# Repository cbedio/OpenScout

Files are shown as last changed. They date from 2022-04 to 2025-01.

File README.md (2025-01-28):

# OpenScout Robot


          
 

## An Open Source Hardware Mobile Robot
OpenScout is a low-cost open source hardware and software mobile robot that can be used for both indoor and outdoor tasks, transporting up to 15kg of payload. The robot is designed to be easily and cheaply (350USD) buildable and modifiable by non-specialists, and to function as a new standard physical platform for robotics research and real-world tasks, replacing current proprietary options. Example applications include last mile and factory floor delivery, site survey and monitoring, and agricultural crop operations.

OpenScout is made of standard sizes aluminium extrusions making it very modular. That means its chassis design depends on the use case and the needs of the user. The robot provides the bare minimum (wizard-of-oz tele-operation and software for controlled differential drive) and future versions will introduce more chassis configurations, ROS/ROS2 integration and gazebo urdf files.

<p align="center" width="100%">
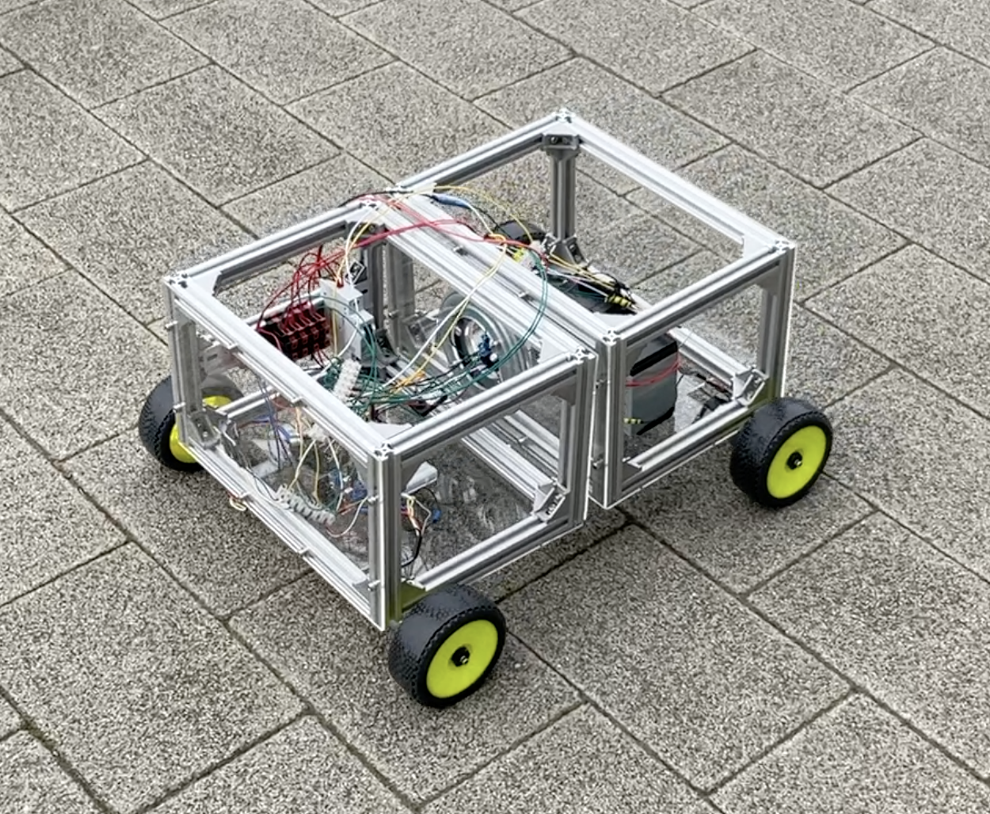
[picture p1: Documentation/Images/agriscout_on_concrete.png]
    
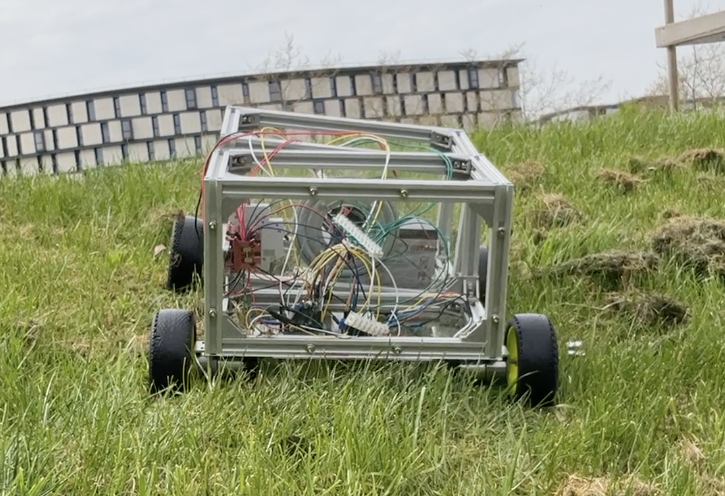
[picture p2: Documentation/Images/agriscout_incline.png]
     
</p>

For detailed changes, see the [CHANGELOG](CHANGELOG.md).

## Demonstration

Demonstrations showing a variety of different mobility aspects can be found in the [Demonstrations](Demonstrations) directory. The below demonstration shows OpenScout with a 'lazy Susan' revolute hinge successfully traversing uneven terrain with circa 40 mm divots.

https://user-images.githubusercontent.com/44243266/164105180-839fc627-df63-4446-af7d-90f431a007b9.mp4

## HackaDay
This project was covered in a [Hackaday article](https://hackaday.com/2022/09/26/robotic-platform-is-open-sourced-and-user-friendly/) by Bryan Cockfield, noting OpenScout as a straightforward and easy build without many specialized tools; providing a really useful platform to expand upon.

## Getting started
Materials used:
The robot consists of 200mm & 300mm 20x20 aluminium extrusions connected with 90 degree angle joints so the width, length and its height can be highly adjustable. We suggest also the [90:1 12V CQrobot](https://www.amazon.co.uk/CQRobot-90-Gearmotor-oz-Diameter/dp/B0887RR8SH) motor with encoder, as 4 of them provide enough traction to carry big payloads. Finally, an Arduino Mega is necessary as it provides enough interrupt pins for the RF receiver and the motor encoders.

The full bill of materials depends on each configuration and for more details please refer to the tutorials.

## Assembly Tutorial:

A fully documented assembly tutorial for the OpenScout with a 'Lazy Susan' revolute hinge is available below. Additionally, a comprehensive and fully annotated [Assembly Manual](Documentation/CAD_Files/Instruction_Manual/InstructionManual.pdf) with step by step 3D projections of the hardware build has been made available to print out. All associated CAD files and schematics are available in the [Documentation](Documentation) directory.

[OpenScout robot with 'Lazy Susan' revolute hinge](Hardware/robot_with_lazy_susan_bearing/README.md)

## How to contribute
While we try to keep this project open source you are free to make your own choice of materials and adapt the robot to your needs. However, we kindly request you to stick to the suggested 200mm & 300mm 20x20 aluminum extrusions, to allow other users disassemble their current configuration and try out yours! If you use OpenScout for your project, please open a PR with your configuration and tutorials. 

The general process of contributing on GitHub is widely documented however the outline process is below:

1. Identify where you want to host the project locally. This could be a OpenScout projects folder for example. 

1. Clone or fork the repository using GitHub desktop or the CLI into this location (CLI is recommended as this helps you become more familiar with Git in general). You can do this with the following command:

    ```bash
    git clone https://github.com/cbedio/OpenScout
    ```

1. Update the project and then make a pull request!

## License

This project is licensed under the [GNU General Public License v3.0](LICENSE) and [CERN-OHL-W](LICENCE) and [CC BY-SA](CC-BY-SA_LICENCE)

<p align="left" width="100%">
    
</p>

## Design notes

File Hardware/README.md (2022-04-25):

# OpenScout Assembly Tutorial

* [OpenScout with Lazy Susan bearing Assembly](robot_with_lazy_susan_bearing/README.md)

<p float="left">
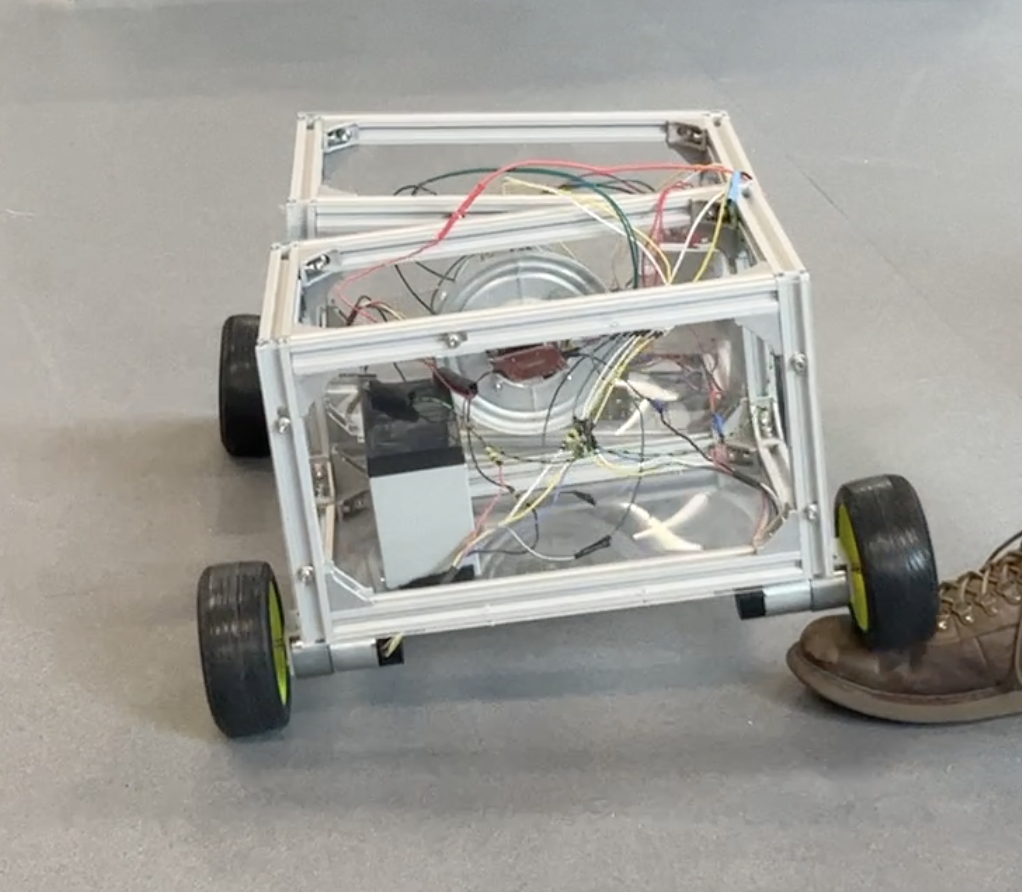
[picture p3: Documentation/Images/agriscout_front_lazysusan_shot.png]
Robot with hinge in the middle configuration
  
</p>

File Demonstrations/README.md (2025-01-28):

# Demonstrations

This folder contains a range of demonstration videos of the OpenScout to showcase its versatility, Lazy Susan mechanism, speed and agility as well as general movement capabilities. Additionally there is a video showing the simulated environment.

## 1 - OpenScout driving over a small slope

https://github.com/user-attachments/assets/b3fbb942-297d-4cb1-b123-8d51ed27b225

## 2 - OpenScout angular rotation

https://github.com/user-attachments/assets/c9248a99-090f-416c-b4d8-dba4bdea5ad4

## 3 - OpenScout moving with no payload

https://github.com/user-attachments/assets/f78b6c29-8d6c-4ecf-929b-bfc48b505c79

## 4 - OpenScout carrying 3kg

https://github.com/user-attachments/assets/6b9834aa-7cd8-4bb6-8bbc-55318a42252c

## 5 - OpenScout carrying 6kg

https://github.com/user-attachments/assets/0d55eaa9-31e6-48b6-9b8e-8ce0252e7a02

## 6 - OpenScout Simulation example run

https://github.com/user-attachments/assets/db36529f-7577-4ad0-a52f-730f6c3506c2

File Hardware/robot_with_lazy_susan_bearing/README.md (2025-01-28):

# Building the OpenScout robot with 'lazy Susan' revolute hinge
This configuration uses four-wheel differential drive steering, and a Lazy Susan hinged body which enables the wheels to drive over small obstacles without the need for suspension.

## Total Build time = 390 minutes (6 hours 30 minutes)

## Assembly Tools Required
These are the tools required to build the OpenScout

| Material | Quantity | UK link |
| ---|---:|:---:|
| M2/3/4/5 Hex Key | 1 | [Link](https://www.amazon.co.uk/ZISHATUO-Hex-Key-Set-2mm-5mm/dp/B09H768WYX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) |
| Small Flathead Screwdriver | 1 | [Link](https://www.amazon.co.uk/Rolson-28852-Screwdriver-Set-Pieces/dp/B00OOTPM6K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) |
| Small Phillips Head Screwdriver | 1 | [Link](https://www.amazon.co.uk/Rolson-28852-Screwdriver-Set-Pieces/dp/B00OOTPM6K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) |
| 100mm Steel rule | 1 | [Link](https://www.amazon.co.uk/Silverline-MT65-Steel-Rule-150/dp/B000LFXRNQ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) |

## Bill of materials
Before proceeding make sure you do have all the following materials. You are encouraged to read carefully the tutorial before starting building the robot.

For the chassis:
| Material | Quantity | Reference | UK link |
| ---|---:|:---:|:---:|
| 300mm 20x20 aluminium extrusion  | 8 |  A1 | [Link](https://ooznest.co.uk/product/v-slot-linear-rail-20x20mm-cut-to-size/) |
| 200mm 20x20 aluminium extrusion  | 17 | A2 | [Link](https://ooznest.co.uk/product/v-slot-linear-rail-20x20mm-cut-to-size/) |
| 20x20 Angle Joint Brace Brackets | 48 | B1 | [Link](https://amz.run/5TF6) |
| 90 Degree Cast Corner | 8 | B2 | [Link](https://ooznest.co.uk/product/90-degree-cast-corner/) |
| 200x340x3mm acrylic sheets | 4 | C1 | [Link](https://www.acrylicsheetcuttosize.co.uk/product/clear-acrylic-sheet/) |
| 240x340x3mm acrylic sheets | 2 | C2 | [Link](https://www.acrylicsheetcuttosize.co.uk/product/clear-acrylic-sheet/) |
| Lazy Susan 5.5in | 1 | LS | [Link](https://amz.run/5TF8) |
| Din rail with terminal blocks | 1 | DT | [Link](https://amz.run/5TFF) |
| Velcro 50mmx1m | 1 | Q | [Link](https://amz.run/5TFP) |
| 90:1 12V motor with encoders | 4 | M1 | [Link](https://amz.run/5TFQ) |
| Wheels (112x46mm) | 4 | M2 | [Link](https://www.amazon.co.uk/best-rubber-hexagon-offroad-crawler/dp/B08B16VQTZ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) |
| Wheel Hex Driver 12mm to 17mm | 4 | M3 | [Link](shorturl.at/axT25) |
| Hex coupler 6mm | 4 | M4 | [Link](https://amz.run/5TFT) |

For the electronics:
| Material | Quantity | Reference | UK link |
| ---|---:|:---:|:---:|
| 12V Lead Acid battery | 1 | E1 | [Link](https://uk.rs-online.com/web/p/lead-acid-batteries/0597835) |
| 10A circuit breaker | 1 | E2 | [Link](https://amz.run/5TFI) |
| Buck converter | 1 | E3 | [Link](https://amz.run/5TFJ) |
| Arduino Mega | 1 | E4 | [Link](https://amz.run/5TFL) |
| L298N Motor drivers | 2 | E5 | [Link](https://amz.run/5TFN) |
| Radio transmitter-receiver | 1 | E6 | [Link](https://amz.run/5TFO) |
| Breadboards | - | - | - |
| Wires | - | - | - |

Bolts & nuts:
| Material | Quantity | Reference | UK link |
| ---|---:|:---:|:---:|
| Sems screw 6mm (More info needed) | 16 | P4.6 | - |
| Sems screw 8mm (More info needed) | 8 | P4.8 | - |
| M4 8mm socket screw | 2 | S4.8 | - |
| M4 10mm socket screw | 8 | S4.10 | - |
| M4 12mm socket screw (More info needed) | 4 | S4.12 | - |
| M4 16mm socket screw (More info needed) | 4 | S4.16  | - |
| M4 30mm socket screw | 4 | S4.30 | - |
| M5 10mm socket screw | 144 | S5.10 | - |
| M4 T-slot nuts | 10 | T4 | - |
| M5 T-slot nuts | 144 | T5 | - |
| M4 Hex nuts | 12 | N1 | - |
| M4 Hammer nuts (More info needed)| 8 | N2 | - |
| M5 Washers | 170 | N3 | - |

<p float="left">
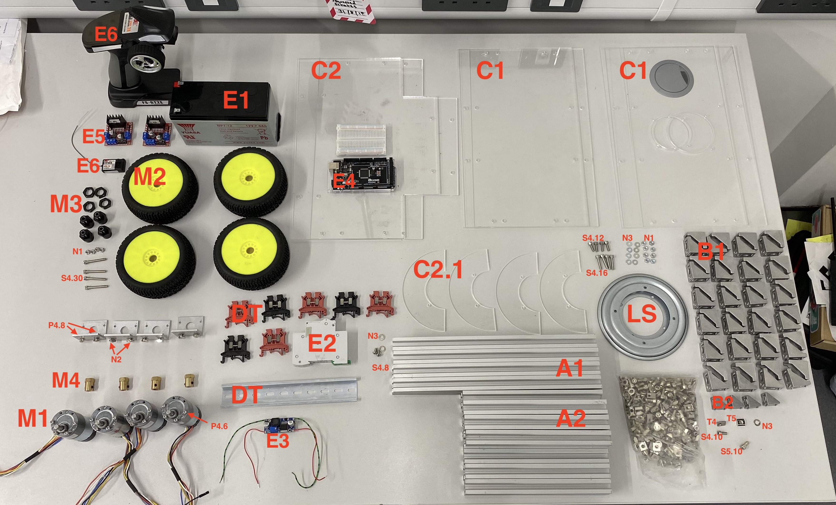
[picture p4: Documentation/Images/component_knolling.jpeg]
Open for full resolution
  
</p>

(**NOTE**: The links provided only as examples and there is no affiliation with the suppliers. The reader is advised to look for cheaper alternatives if possible. The motor brackets are provided in the CQRobot motor package, thus they are not in the bill of materials. Please keep in mind that alternative motors, brackets or components might require different bolts or additional parts.)

## Assembly instructions
This tutorial consists of 7 parts for constructing the robot platform with the hinge in the middle. It is necessary to be followed in the given order. After finishing the assembly, the robot is ready to be flashed with firmware!

Parts:
1. [Front compartment](./front_compartment.md)
2. [Back compartment](./back_compartment.md)
3. [Connecting the two compartments with the hinge](./hinge.md)
4. [Adding the acrylic panels](./acrylic_panels.md)
5. [Din rail](./din_rail.md)
6. [Attaching the motors and the wheels](./motors_and_wheels.md)
7. [Adding the electronics](./circuit_assembly_instructions.md)
8. [Assembling the system](./assembling_the_system.md)

## Adding the software
[Add the PID controller to the Arduino](../../Software/README.md)

## Speed PID controller calibration
[Speed PID controller calibration](./pid_calibration.md)

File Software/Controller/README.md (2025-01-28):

# Flashing Controller Software to the OpenScout Robot

## Install time = 5 minutes

The main script that needs to be uploaded to the Arduino board is located within the `Software` folder of this directory. To upload the sketch we recommend that you use the Arduino IDE, which can be obtained from [arduino.cc](https://www.arduino.cc/en/software).

## Getting started

1. Open the Arduino IDE and load in the `refined_pid.ino` file (`File -> Open -> select_file`).
1. Upload the sketch (see settings below)

### Settings

The firmware can be uploaded through `Sketch -> Upload` or by pressing the upload button.

Connect the Arduino board to the computer and set the port it is attached to:
  
- `Tools -> Board -> Arduino AVR Boards -> *Select the Arduino Board*`
- `Tools -> Processor -> *Select the Arduino Prosessor*`
- `Tools -> Port -> *Select the USB port*`

## Attribution

Github history lost due to moving files.

README.md updated by https://github.com/Rudi-Cato

Twist_via_MQTT.ino created by https://github.com/Rudi-Cato

refined_pid.ino created by https://github.com/Tobies-Cormac

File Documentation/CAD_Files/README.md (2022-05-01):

# Index of files

## DXF Files. These files are used for Laser Cutting

## STEP Files. These files can be modified in generic 3D CAD software

## Instruction Manual. Hard copy instructions for building the robot chassis

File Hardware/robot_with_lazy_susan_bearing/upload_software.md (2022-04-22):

# Flashing Controller Software to the AgriScout Robot

## Install time = 5 minutes

The main script that needs to be uploaded to the Arduino board is located within the `Software` folder of this directory. To upload the sketch we recommend that you use the Arduino IDE, which can be obtained from [arduino.cc](https://www.arduino.cc/en/software).

## Getting started

1. Open the Arduino IDE and load in the `simple_pid.ino` file (`File -> Open -> select_file`).
1. Upload the sketch (see settings below)

### Settings

The firmware can be uploaded through `Sketch -> Upload` or by pressing the upload button.


Connect the Arduino board to the computer and set the port it is attached to:
  
- `Tools -> Board -> Arduino AVR Boards -> *Select the Arduino Board*`
- `Tools -> Processor -> *Select the Arduino Prosessor*`
- `Tools -> Port -> *Select the USB port*`

## What's next?

Follow the [pid calibration](./pid_calibration.md) tutorial to fine tune the PID values for the speed control.

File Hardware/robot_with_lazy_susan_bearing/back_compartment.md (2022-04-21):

# Back Compartment

## Build time = 90 minutes

### Bill of materials:

| Material | Quantity | Reference | UK link |
| ---|---:|:---:|:---:|
| 300mm 20x20 aluminium extrusion  | 4 |  A1 | [Link](https://ooznest.co.uk/product/v-slot-linear-rail-20x20mm-cut-to-size/) |
| 200mm 20x20 aluminium extrusion  | 9 | A2 | [Link](https://ooznest.co.uk/product/v-slot-linear-rail-20x20mm-cut-to-size/) |
| 20x20 Angle Joint Brace Brackets | 24 | B1 | [Link](https://amz.run/5TF6) |
| 90 Degree Cast Corner | 8 | B2 | [Link](https://ooznest.co.uk/product/90-degree-cast-corner/) |
| M4 10mm socket screw | 8 | S4.10 | - |
| M5 10mm socket screw | 72 | S5.10 | - |
| M4 T-slot nuts | 8 | T4 | - |
| M5 T-slot nuts | 72 | T5 | - |
| M5 Washers | 80 | N3 | - |

## Introduction

The back compartment consists of a boxed-shaped construction which is almost identical to the front compartment. Its key difference is that it makes use of one extra (A2) extrusion on the right side of the box, to accommodate the din-rail which will be introduced later on. Also, the (A2) extrusion is fitted and attached using M4 (T4), (S4.10) nuts and screw with slightly smaller (B2) 90 degree joint brackets. The (T4) nut, does not need to be fitted through the open-ended (A2), instead it can be fitted in-place and fasting a screw on it will secure it (The fact that is fitted in-place though can be a bit tricky to properly secure it.)

## Step-by-step instructions

1. Duplicate the front compartment by following the previous tutorial ([front compartment](./front_compartment.md)) up to step 7, before fully connecting the two frames together. Ensure that the frame is constructed at the corners correctly and that the assembled parts look as in the following picture:

<p float="center">
  Attaching the front side with the back side of the back compartment
</p>

2. Attach 2 (B2) joints on each side on the spare (A2) extrusion on the right side of the compartment using the M4 parts. The (T4) nut can be fitted in-place, however adjusting it can be tricky. Try to align it an make it look as in the following picture. Screwing it tightly will hold it in-place as it rotates within the (A2).

3. Attach the piece prepared in the previous step on the construction. (Hint: A smaller allen key might help the ones with not so delicate hands.)

<p float="center">
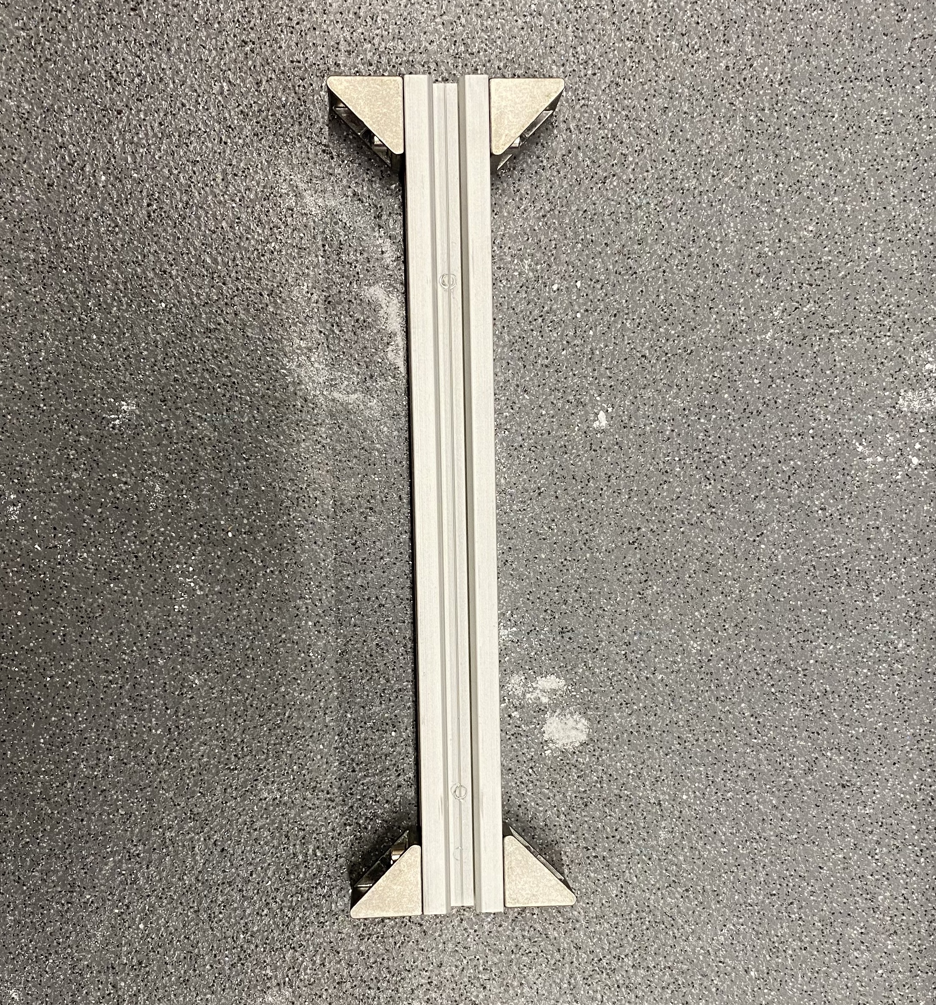
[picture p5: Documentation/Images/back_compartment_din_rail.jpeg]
This piece will host the din rail
  
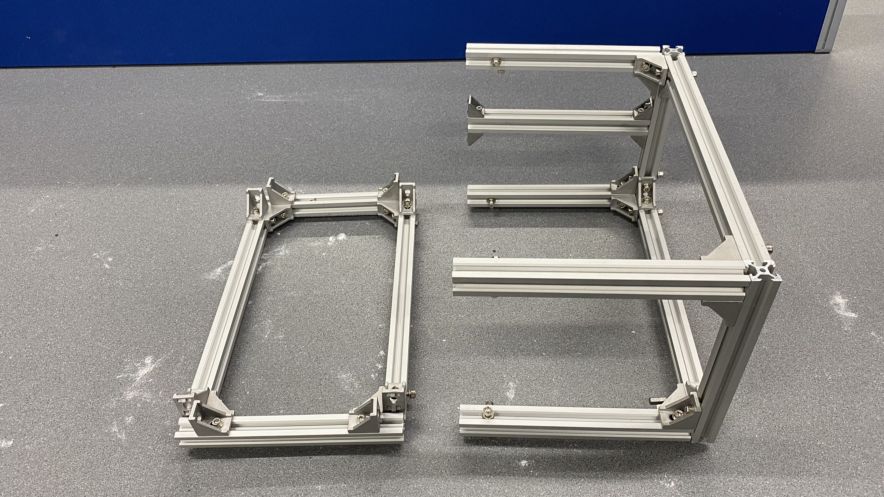
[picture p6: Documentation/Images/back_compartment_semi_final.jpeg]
Attaching the front side with the back side of the back compartment
  
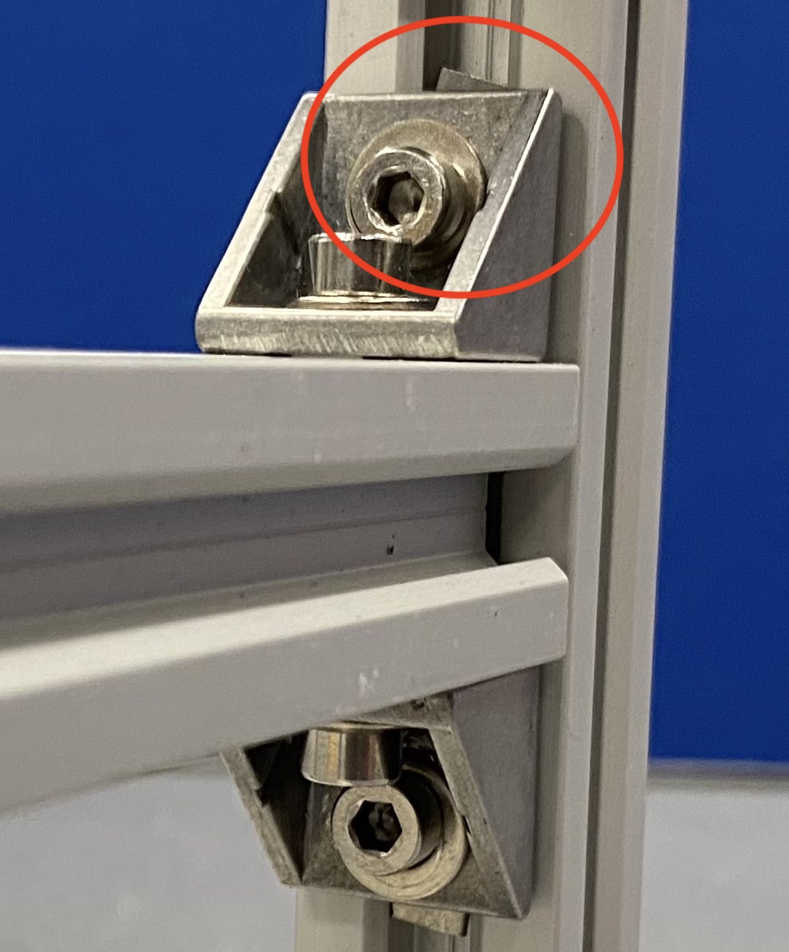
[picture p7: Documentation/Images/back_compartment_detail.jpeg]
Dir rail in detail
  
</p>

4. Fit the two frames together and tight the bolts together.
<p float="center">
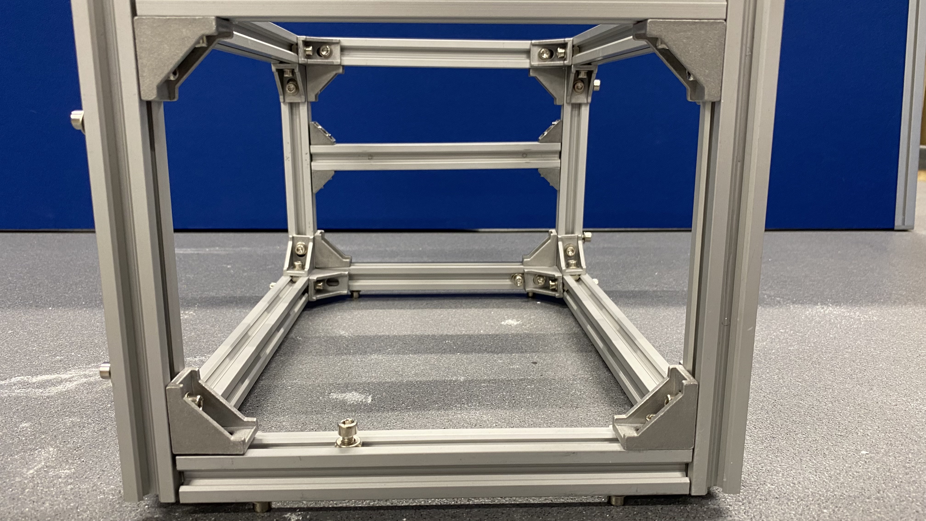
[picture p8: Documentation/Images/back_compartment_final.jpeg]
The back compartment fully assembled.
  
</p>

## What's next?
Follow the [lazy susan hinge](./hinge.md) tutorial to connect the front and the back compartment.

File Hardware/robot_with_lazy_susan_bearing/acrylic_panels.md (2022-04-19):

# Acrylic panels

## Build time = 20 minutes

### Bill of materials:

| Material | Quantity | Reference | UK link |
| ---|---:|:---:|:---:|
| 200x340x3mm acrylic sheets | 4 | C1 | [Link](https://www.acrylicsheetcuttosize.co.uk/product/clear-acrylic-sheet/) |
| 240x340x3mm acrylic sheets | 2 | C2 | [Link](https://www.acrylicsheetcuttosize.co.uk/product/clear-acrylic-sheet/) |

## Introduction

This tutorial includes instructions to laser-cut and fit the bare minimum acrylic panels needed on the robot. That is on the bottom, front and back side of the robot; in the previous tutorial, 2 sheets also were added in the middle as the hinge is attached on them. The reason is to keep the cost to the minimum, however the 3mm is not that strong as it should. You are welcome to use 5mm acrylic sheets, something stronger, or even wood to take full advantage of the maximum robot's payload.

## Step-by-step instructions

1. TODO: 
 - how to laser cut the bottom, front and back panels.
 - Upload the .dxf files in the `Documentation/CAD_Files` folder
 - Update the `Documentation/CAD_Files/README.md`

2. Fit the side panels (the smaller ones) as in the previous tutorial using the already equipped (S5.10) screws. (**HINT**: Fit first two opposing sides, and slide the panel across the extrusion, so you can align the misaligned (T5) nuts.)

<p float="center">
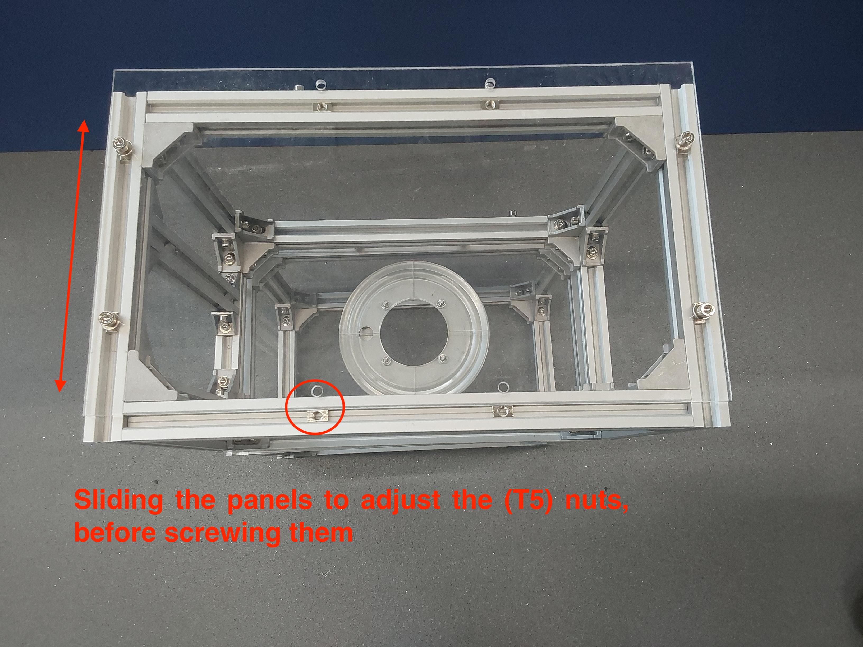
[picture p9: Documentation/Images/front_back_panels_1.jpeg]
Attaching the side panels
  
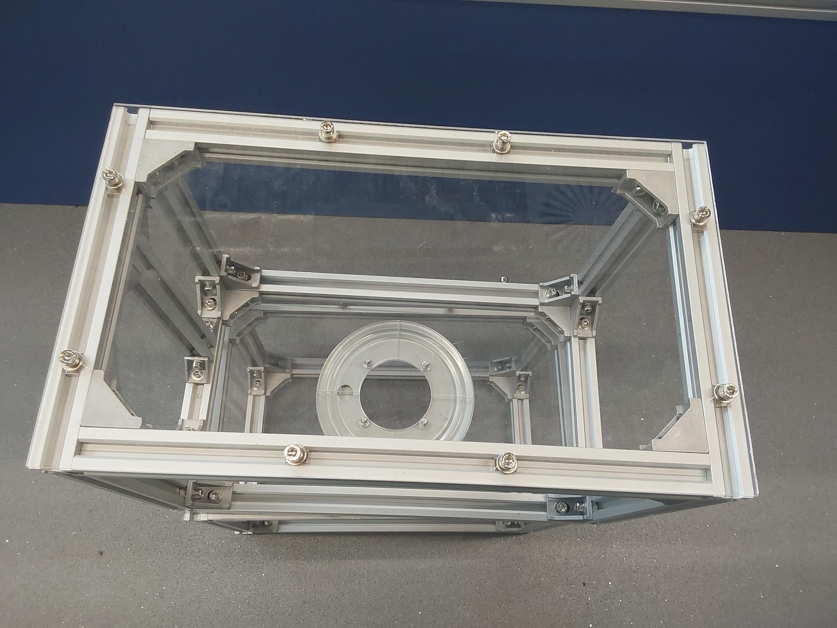
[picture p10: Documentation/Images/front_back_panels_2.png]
Attaching the side panels
  
</p>

3. Fit the bottom panels (the bigger ones) as in the previous step using the already equipped (S5.10) screws. The motor slots should be facing away from the middle. Repeat for each half of the construction. Make sure the construction is solid before progressing.

<p float="center">
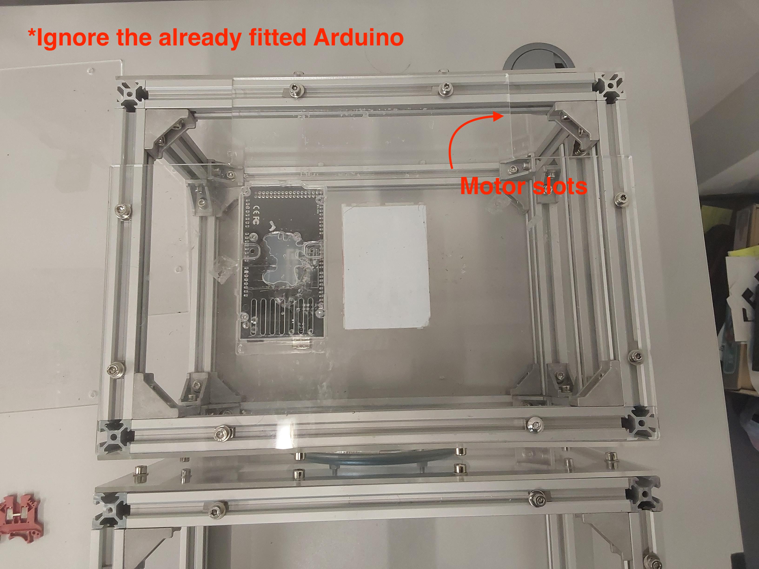
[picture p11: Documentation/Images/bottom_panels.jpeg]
Attaching the bottom panels
  
</p>

## What's next?

Follow the [din rail](./din_rail.md) tutorial to connect the front and the back compartment.

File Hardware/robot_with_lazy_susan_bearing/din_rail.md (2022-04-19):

# Din rail

## Build time = 15 minutes

### Bill of materials:

| Material | Quantity | Reference | UK link |
| ---|---:|:---:|:---:|
| Din rail with terminal blocks | 1 | DT | [Link](https://amz.run/5TFF) |
| Din rail with terminal blocks | 1 | DT | [Link](https://amz.run/5TFF) |
| 10A circuit breaker | 1 | E2 | [Link](https://amz.run/5TFI) |
| M4 8mm socket screw | 2 | S4.8 | - |
| M4 T-slot nuts | 2 | T4 | - |
| M5 Washers | 2 | N3 | - |

## Introduction

The din rail (DT) consists of a holed metal with some terminal blocks (red & white) attached on it. You can attach as many as you wish, and its purpose is provide some convience while wiring the battery.

## Step-by-step instructions

1. Attach the terminal blocks and the circuit breaker (E2) on the (DT). They 'click' if fitted properly, and they freely move along the rail.

<p float="center">
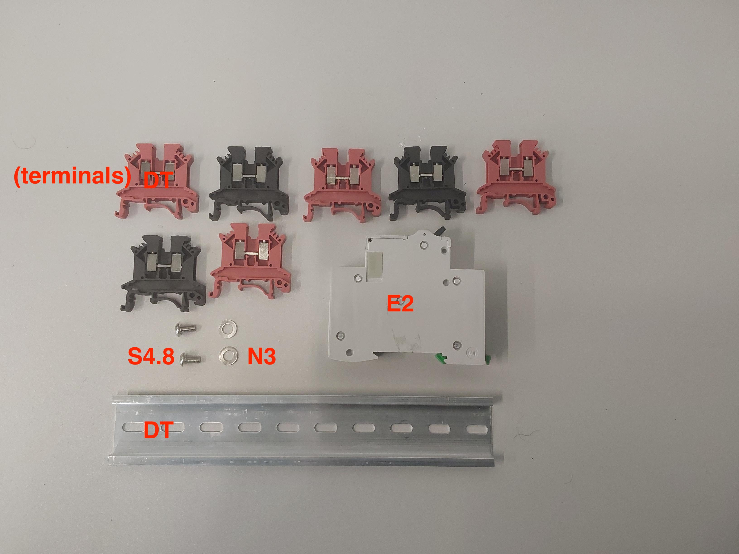
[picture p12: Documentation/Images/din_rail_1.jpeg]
Attaching the terminal blokcs on the din rail.
  
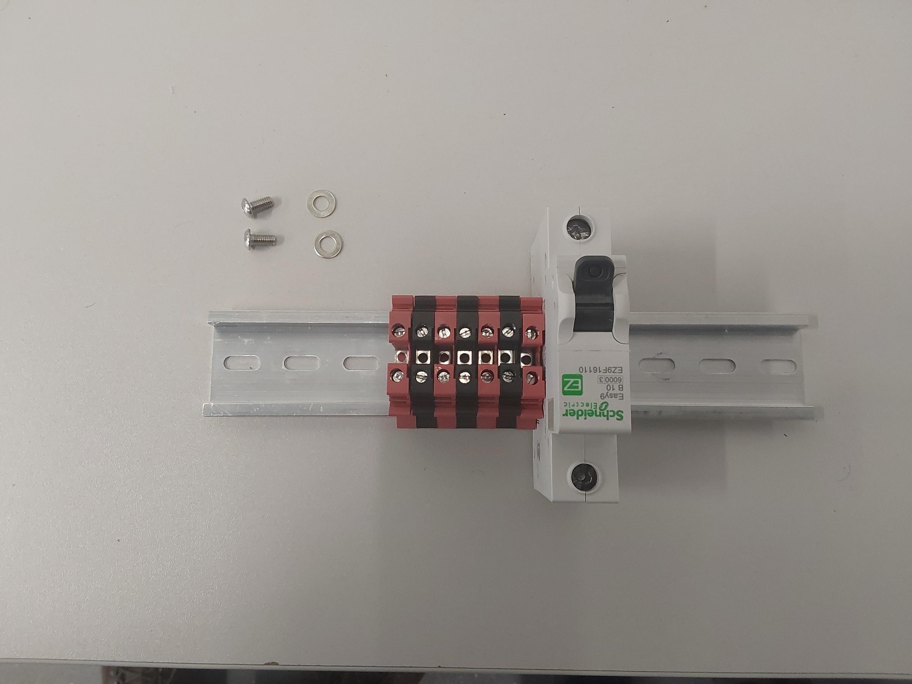
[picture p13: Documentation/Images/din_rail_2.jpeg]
The din rail assembled
  
</p>

2. Fit in-place 2 (T4) nuts on the extrusion that will accommodate the din rail and screw the rail on them using (N3) washers. Make sure that is properly fitted by giving it a shake.

<p float="center">
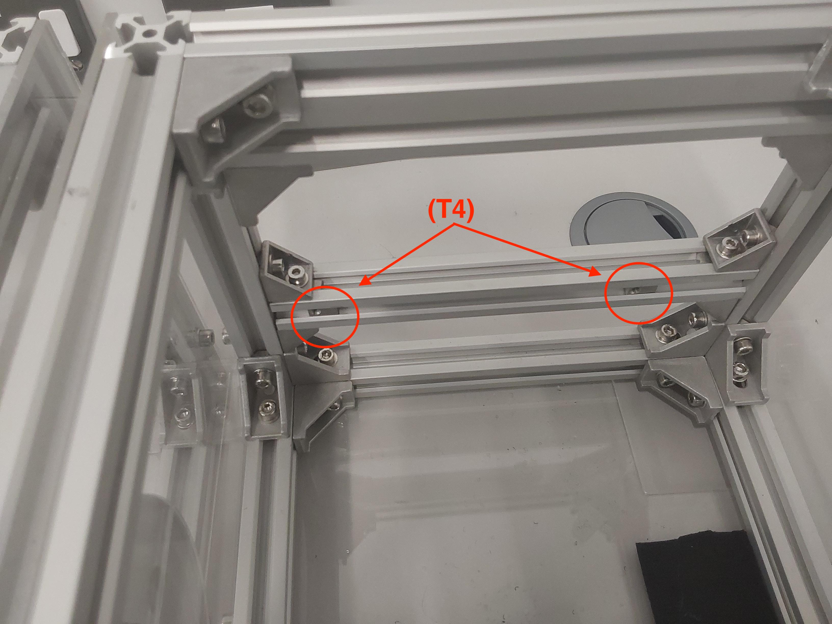
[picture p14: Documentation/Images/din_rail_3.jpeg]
Attaching the terminal blokcs on the din rail.
  
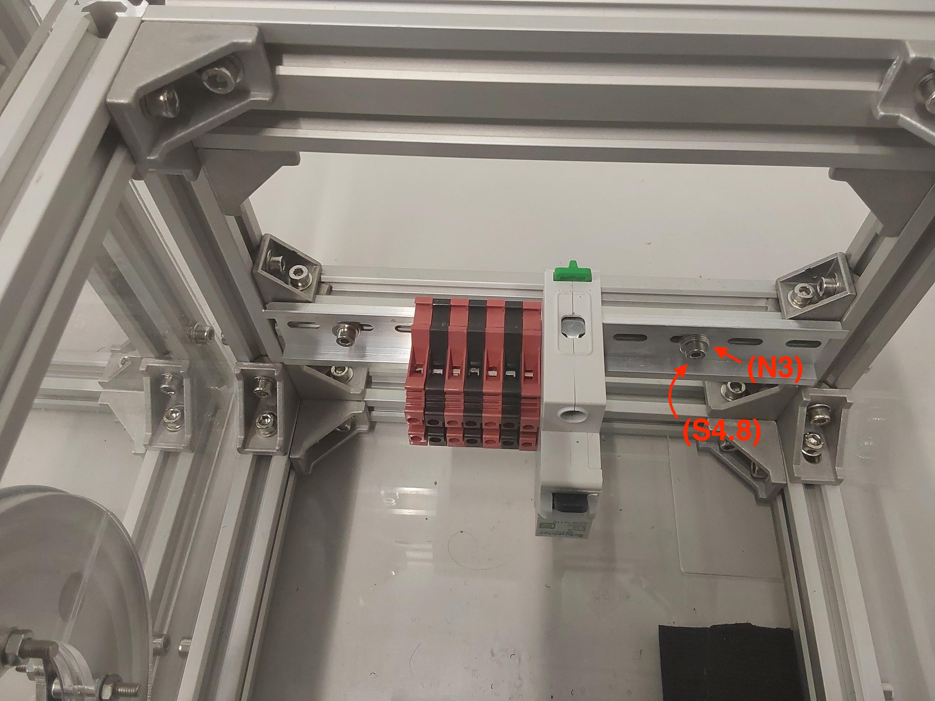
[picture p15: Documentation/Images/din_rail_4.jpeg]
The din rail assembled
  
</p>

## What's next?
Follow the [attaching motors and wheels](./motors_and_wheels.md) tutorial to complete the chassis of the robot.

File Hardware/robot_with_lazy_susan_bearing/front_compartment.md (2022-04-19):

# Front Compartment

## Build time = 75 minutes

### Bill of materials:

| Material | Quantity | Reference | UK link |
| ---|---:|:---:|:---:|
| 300mm 20x20 aluminium extrusion  | 4 |  A1 | [Link](https://ooznest.co.uk/product/v-slot-linear-rail-20x20mm-cut-to-size/) |
| 200mm 20x20 aluminium extrusion  | 8 | A2 | [Link](https://ooznest.co.uk/product/v-slot-linear-rail-20x20mm-cut-to-size/) |
| 20x20 Angle Joint Brace Brackets | 24 | B1 | [Link](https://amz.run/5TF6) |
| M5 10mm socket screw | 72 | S5.10 | - |
| M5 T-slot nuts | 72 | T5 | - |
| M5 Washers | 72 | N3 | - |

<p float="left">
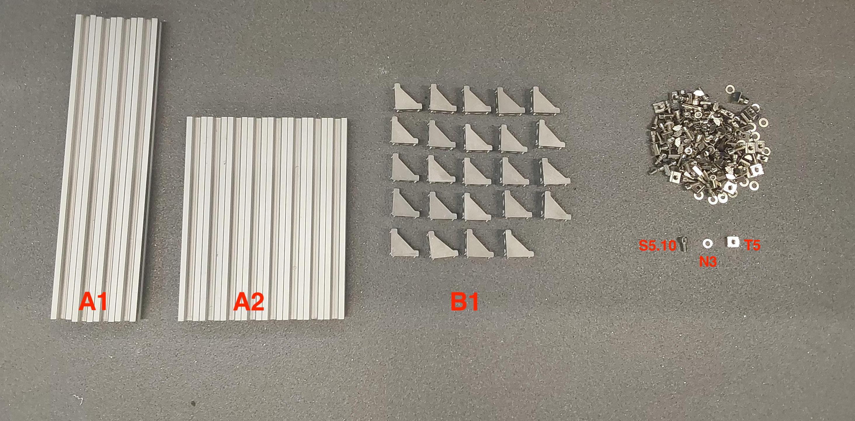
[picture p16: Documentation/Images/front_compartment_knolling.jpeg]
Open for full resolution
  
</p>

## Introduction

The front compartment consists of a boxed-shaped construction made of x4 300mm aluminium extrusions (A1) in horizontal positions (giving width to the box), x4 200mm (A2) extrusions (giving length to the box) and x4 (A2) extrusions vertically attached (giving height to the box). The following image shows how it should look like if completed successfully. Notice how the extrusions are attached together using 3 angle joints (red circle) (B1) on each corner (8 corners in total). Furthemore, the compartment is symmetrical across all 3 major axis. The blue circles indicate bolts which will accommodate the acrylic panels (8 bolts in total in the bottom, front and back sides of the compartment. The top and the left/right sides do not accommodate acrylic panels currently to lower the cost.).

Final result:
<p float="left">
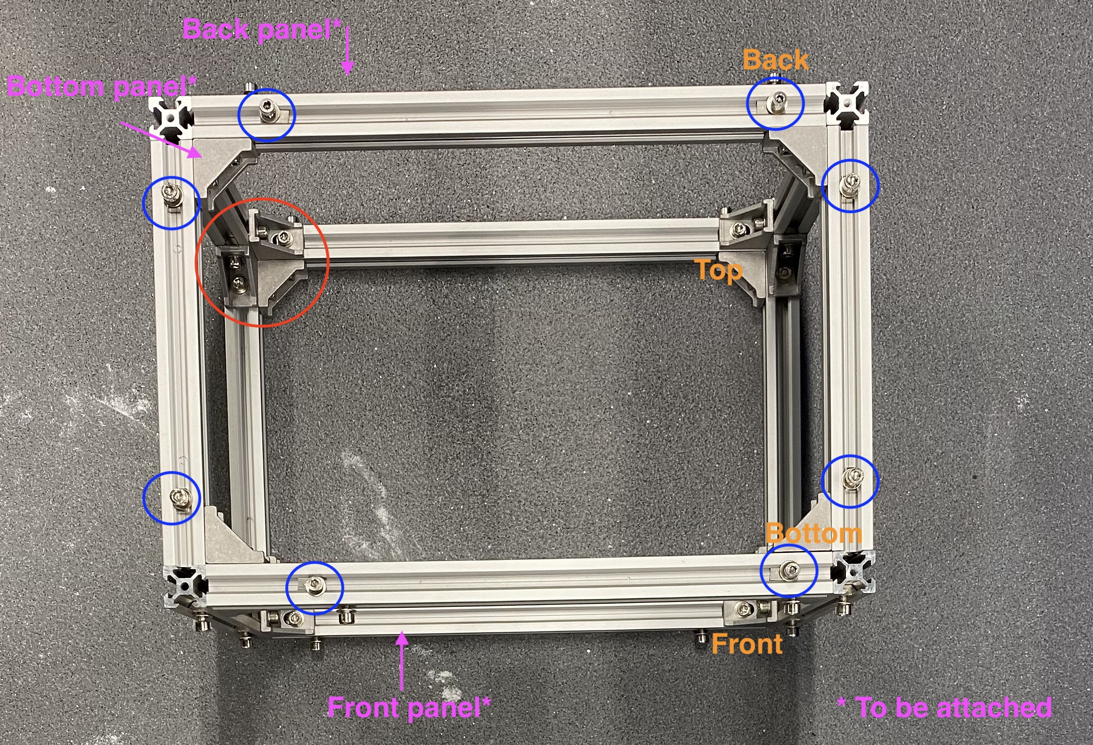
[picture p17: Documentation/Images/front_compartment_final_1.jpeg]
Resulting front compartment
  
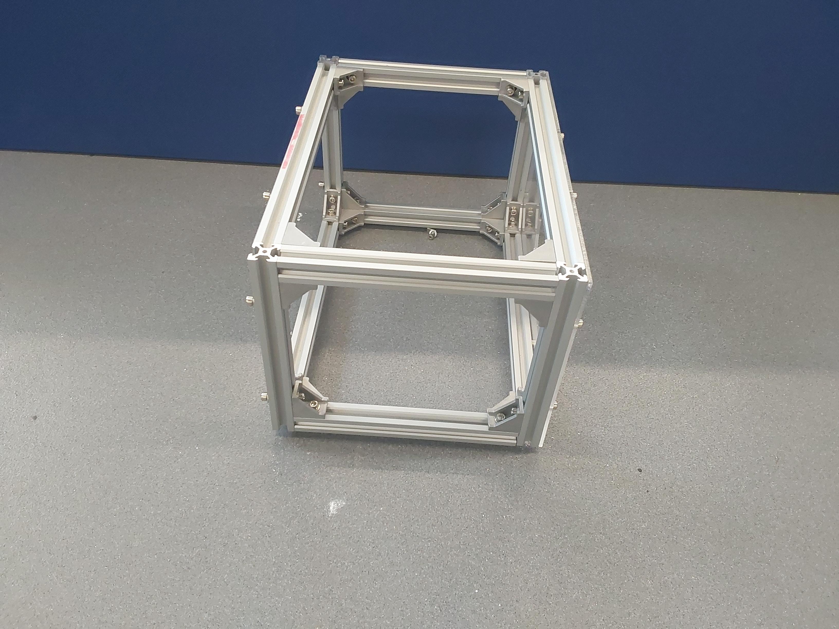
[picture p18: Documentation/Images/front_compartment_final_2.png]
Resulting front compartment
  
</p>

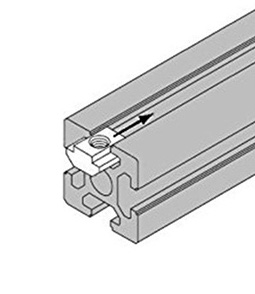
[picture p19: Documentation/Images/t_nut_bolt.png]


The T-slot nut (T5) is very useful to fasten things on aluminium extrusions as it allows it to freely slide within the extrusion and gets secured once it's fastened with a screw. The order of attachment from bottom to top should be: T-slot nut (T5), attachment, washer (N3) and lastly secured with the bolt (S5.10). **Be careful though that the T-nut to be inserted needs an open ended extrusion, so you need to know how many of them you need before start attaching things to the end of the extrusions.**

## Step-by-step instructions

1. Prepare 4 (A2) extrusions which are going to be used vertically defining the height of the robot. Attach the (B1) joints using the order defined previously: (T5) nut, (B1) joint, (N3) washer, and secure with a (S5.10) socket screw. Each side should have 2 joints attached and a (S5.10) without something attached (these sockets will later accommodate the acrylic panels). Do not tight the screws too much as this is not their final place. Just try to secure them on the aluminium.

<p float="center">
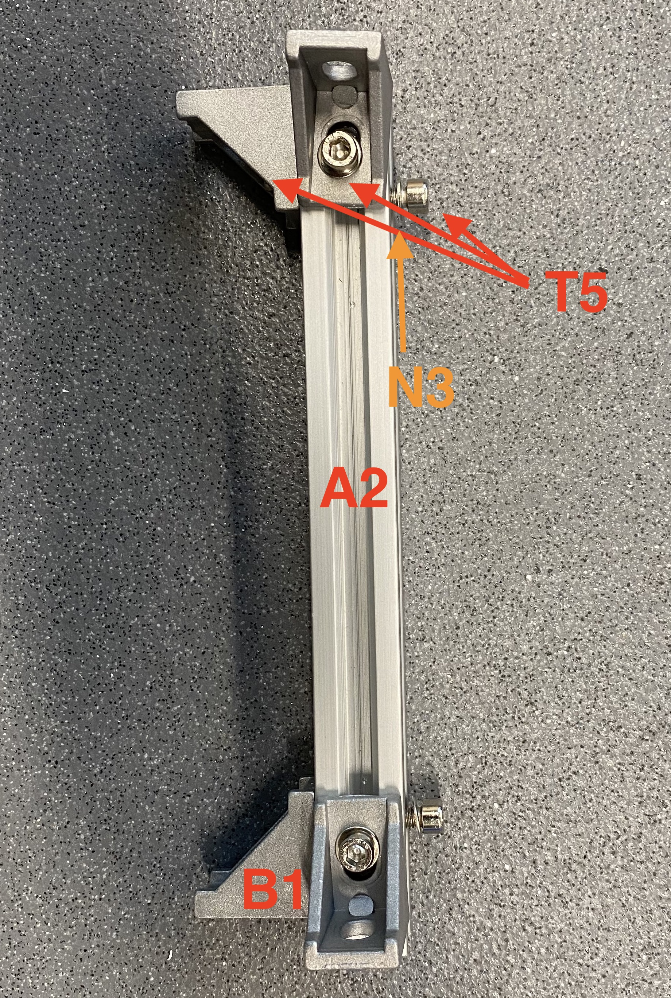
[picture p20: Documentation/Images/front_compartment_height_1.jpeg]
This will be fitted vertically on the robot
  
  Prepare 4 of these
</p>

2. Prepare 2 more (A2) extrusions to secure (T5) nuts, (N3) washers and (S5.10) screws; 3 on each side as in the following image. Again, do not over tighten (finger tight is good enough so they don't fall out of the channel), as they are later going to accommodate the bottom acrylic panels, and the (B1) joints we prepared in the previous step.

<p float="center">
  This will be fitted horizontally on the bottom part of the robot
  Prepare 2 of these
</p>

3. Prepare 2 off (A2) extrusions and secure using (T5) nuts, (N3) washers and (S5.10) screws; 2 on each side this time. Again, do not over tighten, they are later going to be used as the ones in step 2, but on the top side which will not host any acrylic (hence the 2 instead of 3 screws).

<p float="center">
  This will be fitted horizontally on the top part of the robot
  Prepare 2 of these
</p>

4. Prepare 2 off (A1) extrusions which are going to be used horizontally (on the top side) defining the width of the robot. See the following image for reference.

<p float="center">
  This will be fitted horizontally on the top part of the robot
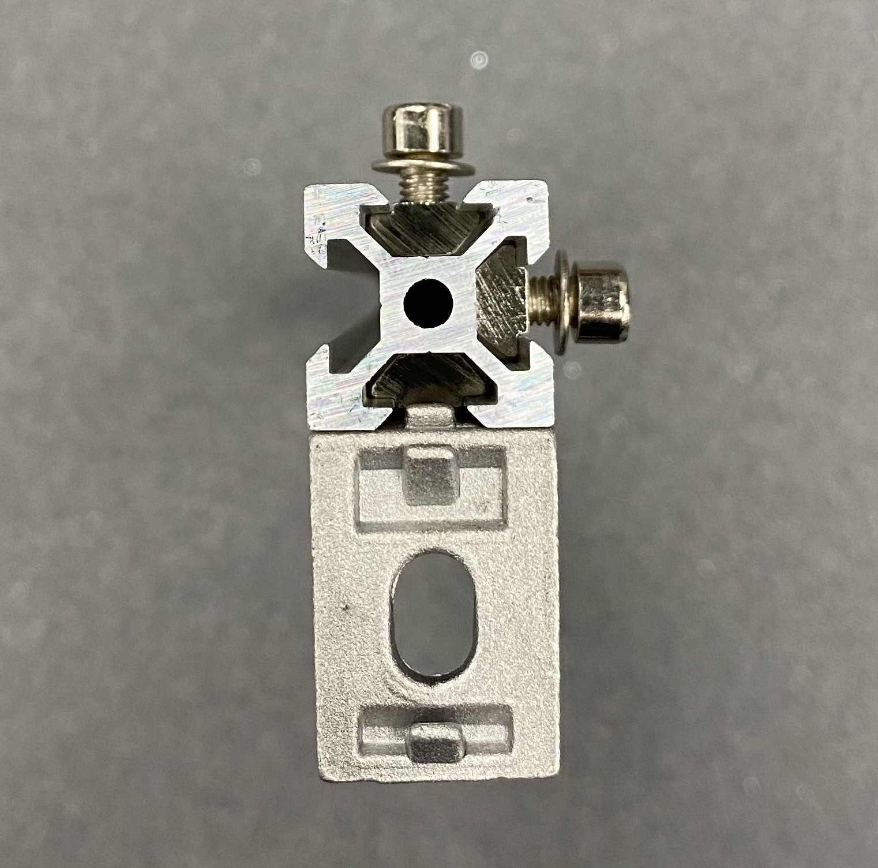
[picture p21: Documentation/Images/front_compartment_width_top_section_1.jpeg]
  
</p>

5. Prepare the rest 2 (A1) extrusions which are going to be used horizontally (on the bottom side) defining the width of the robot. See the following image for reference. In contrast with step 4, each side has 3 (S5.10) screws, as the extra one is going to secure the bottom panel.

<p float="center">
  This will be fitted horizontally on the top part of the robot
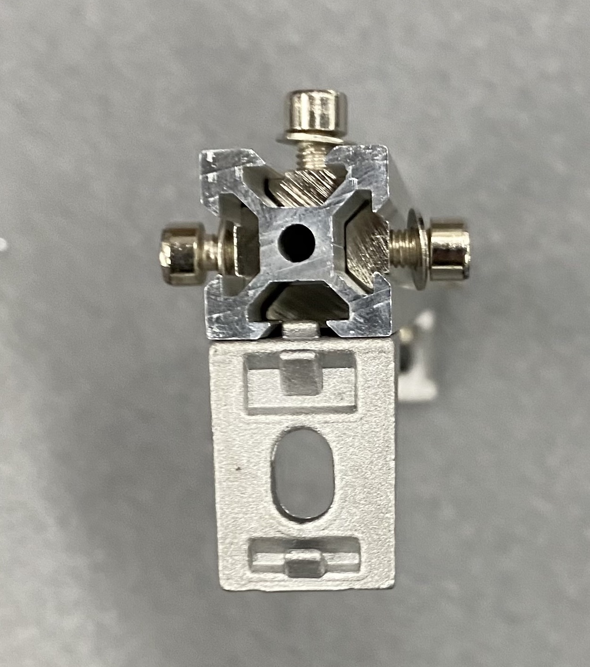
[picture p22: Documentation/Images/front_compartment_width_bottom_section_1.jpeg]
  
  All the components prepared
</p>

6. To assemble the front side frame, you need to attach together 2 pieces from step 1, and with one piece from step 4. and one piece from step 5. See the following image for reference. To attach them together you will need to unscrew some screws to attach the (B1) on the piece, and untight some others to align them. Be careful while untightening as the (T5) nuts might fall off the extrusion. You can now fully tighten the properly aligned (S5.10) screws, as this is their final position. Repeat the step to form the back side of the frame.

<p float="center">
  The front side of the compartment
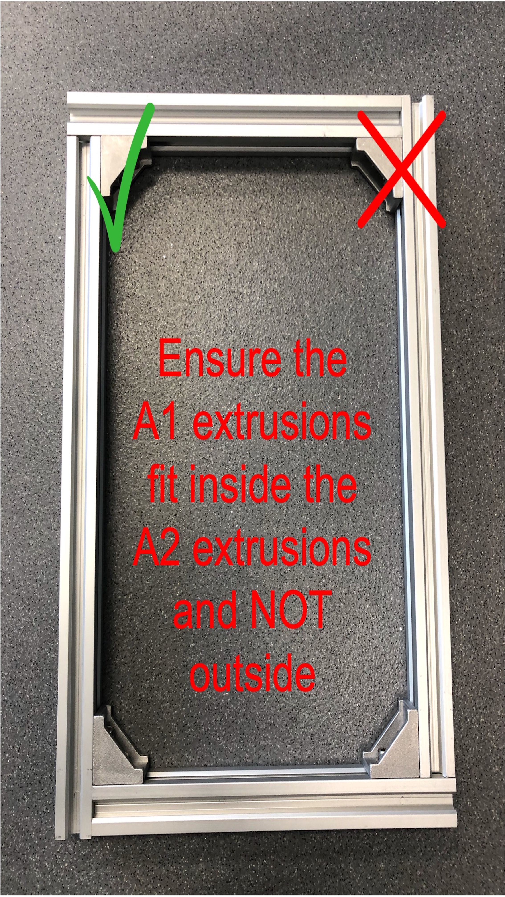
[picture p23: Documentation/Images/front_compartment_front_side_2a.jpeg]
  
  Prepare 2 of these
</p>

7. Connect the two frames together using the extrusions we prepared in step 2. and in step 3. The pieces prepared in step 2 (with the extra (S5.10) screws), should be on the same side with the pieces prepared in step 5. as they will accommodate the acrylic panel and they should be 8 in total. Make sure to tight the screws after aligning the frame.

<p float="center">
  Attaching the front side with the back side of the compartment
</p>

If everything was followed correctly, the box should look as the reference image in the beginning of the page. If not, don't worry, everything can be fixed with in-place adjustments.

(**HINT**: It might be hard remembering which screws has been tightened and which not. Marking them with a sharpie or with a bit of tape after tightening them might help.)

## What's next?
Follow the [back compartment](./back_compartment.md) tutorial for the back side of the robot.

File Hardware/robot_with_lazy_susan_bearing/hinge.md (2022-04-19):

# Adding the Lazy Susan hinge

## Build time = 45 minutes

### Bill of materials:

| Material | Quantity | Reference | UK link |
| ---|---:|:---:|:---:|
| 200x340x3mm  acrylic sheet | 2 | C1 | [Link](https://www.acrylicsheetcuttosize.co.uk/product/clear-acrylic-sheet/) |
| Spacers from acrylic leftovers | 2 | C2.1 | [Link](https://www.acrylicsheetcuttosize.co.uk/product/clear-acrylic-sheet/) |
| Lazy Susan 5.5in | 1 | LS | [Link](https://amz.run/5TF8) |
| M4 12mm socket screw (More info needed) | 4 | S4.12 | - |
| M4 16mm socket screw (More info needed) | 4 | S4.16  | - |
| M4 Hex nuts | 8 | N1 | - |
| M5 Washers | 8 | N3 | - |

Note: The (C2.1) components have been cut using leftovers from the 3mm acrylic sheet.

## Introduction

This tutorial includes instructions to connect the front and the back compartments using the hinge.

## Step-by-step instructions

1. TODO:
 - how to laser-cut the middle panels..
 - Upload the .dxf files in the `./cad_files` folder
 - Update the `./cad_files/README.md`

2. Fit the acrylic panel with the bigger hole in back side of the front compartment (the front and the back sides of the compartment are symmetrical), using the pre-fitted (S5.10) screws. Next, fit the acrylic panel with the smaller hole on the front side of the back compartment (the din-rail should be located on the right side of the back compartment). When tightening, ensure that diametrically apposite nuts are tightened in sequence (like you would a car wheel), to ensure even compression and reduce potential cracking.

<p float="center">
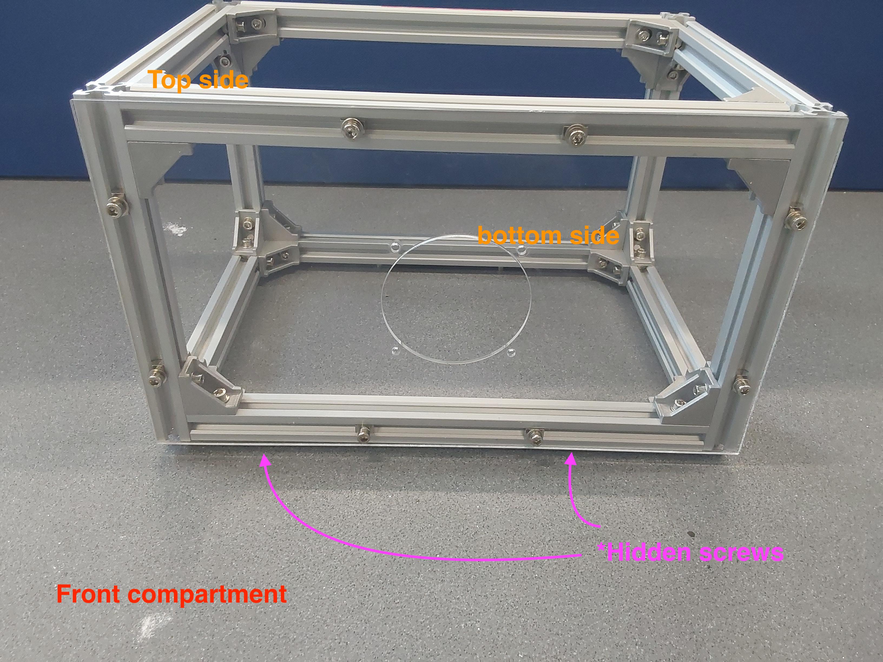
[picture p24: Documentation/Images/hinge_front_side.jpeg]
The front compartment
  
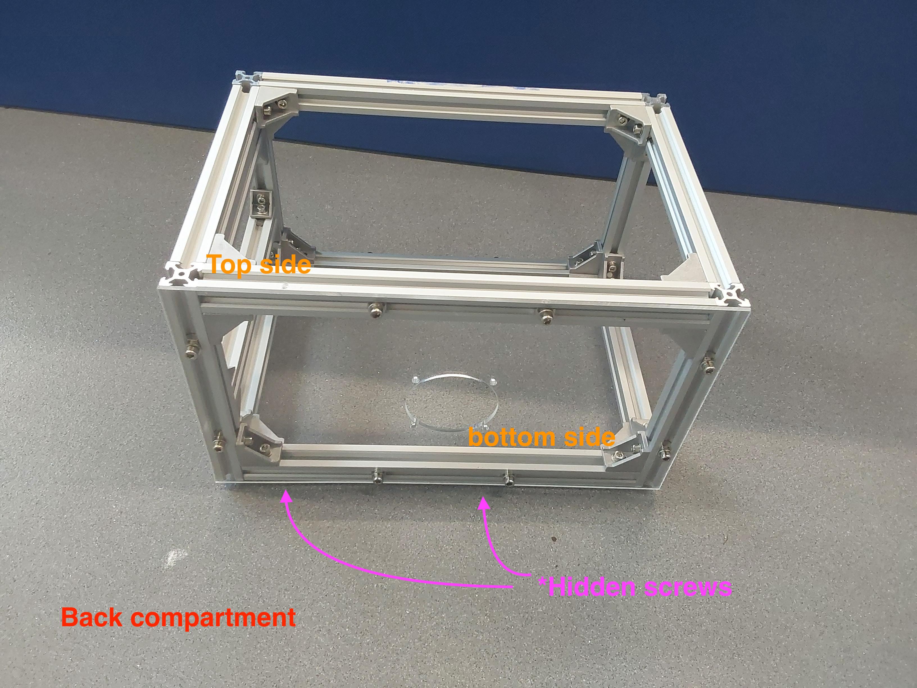
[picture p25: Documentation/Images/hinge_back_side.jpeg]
The back compartment
  
</p>

3. Attach the small hole of the hinge (LS) on the front compartment using the (S4.12) screws; The small hole on the hinge will help screw all of them, by rotating it to each hole.

<p float="center">
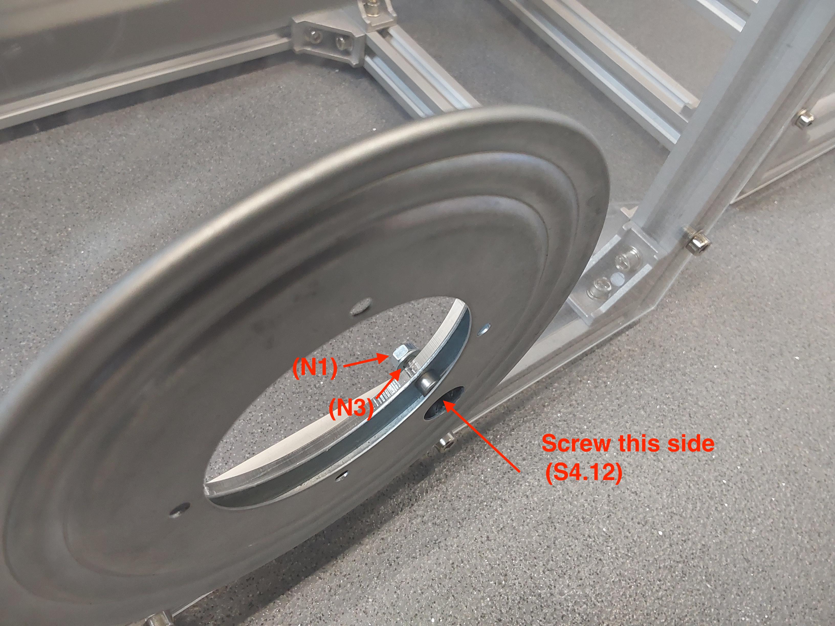
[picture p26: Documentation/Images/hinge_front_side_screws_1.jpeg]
Attaching the hinge on the front side
  
  Attaching the hinge on the front side
</p>

4. Insert 4 (S4.16) screws on top of 4 (N3) washers on the other side of the lazy susan (LS) and attach the spacers (C2.1) in alternating directions.

<p float="center">
  Attaching the hinge on the front side
  Attaching the hinge on the front side
</p>

5. Bring the spacers (C2.1) together forming circles and place them on top of each other in alternating directions. See the following image for reference.

<p float="center">
  Attaching the hinge on the back side
  Attaching the hinge on the back side
  Attaching the hinge on the back side
</p>

6. Finally attach the back compartment and screw the (S4.16) screws using the rest (N1) nuts. Make sure that the compartments can freely move independently.

 <p float="center">
  Attaching the hinge on the back side
</p>

## What's next?
Follow the [acrylic panels](./acrylic_panels.md) tutorial to attach the side and bottom panels on the robot.

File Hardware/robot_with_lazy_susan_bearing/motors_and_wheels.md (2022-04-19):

# Motors and wheels

## Build time = 45 minutes

### Bill of materials:

| Material | Quantity | Reference | UK link |
| ---|---:|:---:|:---:|
| 90:1 12V motor with encoders | 4 | M1 | [Link](https://amz.run/5TFQ) |
| Wheels (112x46mm) | 4 | M2 | [Link](shorturl.at/cwxR2) |
| Wheel Hex Driver 12mm to 17mm | 4 | M3 | [Link](shorturl.at/axT25) |
| Hex coupler 6mm | 4 | M4 | [Link](https://amz.run/5TFT) |
| Sems screw 6mm (More info needed) | 16 | P4.6 | - |
| Sems screw 8mm (More info needed) | 8 | P4.8 | - |
| M4 30mm socket screw | 4 | S4.30 | - |
| M4 Hex nuts | 12 | N1 | - |
| M4 Hammer nuts (More info needed)| 8 | N2 | - |
| M5 Washers | 8 | N3 | - |

## Introduction

We used four 12V 90:1 CQrobot motors as they provide a relatively good amount of torque and they come with encoders as well. The particular motors come with brackets, thus mounting them gets very easy.
One the other hand, the wheels selection wasn't very sophisticated, and soon they will replaced by bigger ones in order to increase ground clearence.

## Step-by-step instructions

1. Fit the motor bracket on the slots on the acrylic, by fitting in-place 2 (N2) nuts and (N3) washers using the (P4.8) screws. Ensure that the (N2) nuts are correctly secured in the channel slot. Repeat for the rest of the motors and make sure that the brackets are properly fitted by shaking them.

<p float="center">
  Attaching the motor brackets on the bottom of the chassis.
  Attaching the motor brackets on the bottom of the chassis.
  Attaching the motor brackets on the bottom of the chassis.
</p>

2. Align the (M1) motor on the bracket using the holes as a guide, and attach them using the (P4.6) screws. Repeat for the rest of the motors.

<p float="center">
  Attaching the motors on the motor brackets.
  Attaching the motors on the motor brackets.
  Attaching the motors on the motor brackets.
</p>

3. Attach the (M4) hex couplers on each motor shaft using the provided screws, and tight them. Ensure that the grub screw is tightened on the flat provided on the motor shaft. Make sure you give enough distance (~10mm) so the wheels won't touch the bracket while driving. Be sure that the hex coupler has been mounted properly by trying to pull it off.

<p float="center">
  Attaching the hex couplers on the motor brackets.
  Attaching the hex couplers on the motor brackets.
  Attaching the hex couplers on the motor brackets.
</p>

4. Attach the (M3) hex adaptors on each wheel so they can be fitted on the (M4) hex couplers. (**Optional**: If you intend driving the robot on surfaces with high friction, you can tape the wheels avoiding fast wear and tear.)

<p float="center">
  Attaching the hex adaptors on the wheels.
  Taping the wheels to avoid damaging them.
</p>

5. Fit the wheels on the shafts using the (S4.30) screws. If the screw does not fully screw on the (M4) hex coupler, use a (N1) hex nut as spacer.

<p float="center">
  Mounting the wheels on the shafts.
</p>

## What's next?
Congratulations! The robot chassis is complete. Follow the [adding the electronics](./circuit_assembly_instructions.md) tutorial to proceed with the wiring.

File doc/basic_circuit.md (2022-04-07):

# Basic electronics layout

Bill of materials:
| Material | Quantity | Reference | UK link |
| ---|---:|:---:|:---:|
| 12V Lead Acid battery | 1 | E1 | [Link](https://uk.rs-online.com/web/p/lead-acid-batteries/0597835) |
| 10A circuit breaker | 1 | E2 | [Link](https://amz.run/5TFI) |
| Buck converter | 1 | E3 | [Link](https://amz.run/5TFJ) |
| Arduino Mega | 17 | E4 | [Link](https://amz.run/5TFL) |
| L298N Motor drivers | 2 | E5 | [Link](https://amz.run/5TFN) |
| Radio transmitter-receiver | 1 | E6 | [Link](https://amz.run/5TFO) |
| 90:1 12V motor with encoders | 4 | M1 | [Link](https://amz.run/5TFQ) |
| Din rail with terminal blocks | 1 | DT | [Link](https://amz.run/5TFF) |
| Velcro 50mmx1m | 1 | Q | [Link](https://amz.run/5TFP) |
| Breadboards | - | - | - |
| Wires | - | - | - |

CQrobot Motor (M1) pinout:
| Motor (M1) | wire |
| ---|-----:|
| ENC_A  | yellow |
| ENC_B  | white |
| VCC | blue |
| GND | gray |
| MOTOR+ | red |
| MOTOR- | black |

## Introduction

This tutorial provides instructions for wiring together the electronic components. Example photos are provided and can be used as reference, however some of the components are optional (e.g. the terminal blocks (DT) on the din rail, and the breadboards) but you are free to replace them with other components such as veroboards, depending on your soldering experience. The schematics provided in `.pdf` format show in-detail how the different components are connected together. (**WARNING**: Please handle the Lead Acid battery (E1) with care.)

## Step-by-step instructions

### 1. Connecting the arduino

1. Attach a strap of velcro (Q) either on the back or the front of the robot (depending on where you'd like to place the battery), and on the bottom of the battery (E1) so you can secure it on the robot. You can use the terminal blocks on the din rail (DT) to prepare some 12V and 5V (using the step down converter (E3)) power lines to power the components.

2. See the [arduino layout](../schematics/arduino_layout.pdf) schematic for reference.

<p float="center">
  Attaching the motor brackets on the bottom of the chassis.
</p>

### 2. Attaching the radio receiver

1. Power the radio receiver (E6) using 5V from the step down converter (E3)
2. Connect radio receiver (E6) channels on the arduino (E4) as follows:

| radio receiver (E6) | Pin on Arduino |
| ---|---:|
| CH1_S | D2 |
| CH2_S | D3 |

3. See the [radio receiver layout](../schematics/rc_layout.pdf) schematic for reference.

### 3. Connecting the front motors with the front motor driver

1. Connect the L298N front motor driver (E5) on 12V and the enable/input pins on the arduino (E4)

| L298N front motor driver (E5) | Pin on Arduino |
| ---|---:|
| ENA | D10 |
| IN1 | D27 |
| IN2 | D26 |
| IN3 | D29 |
| IN4 | D28 |
| ENB | D11 |

2. Connect the output pins of the L298N (E5) on the LF and RF motors (M1) (see the motor color table on the top of the page).

| L298N front motor driver (E5) | RF Motor (M1)|
| -----|----:|
| OUT1 | red |
| OUT2 | black |

| L298N front motor driver (E5) | LF Motor (M1)|
| -----|----:|
| OUT3 | black |
| OUT4 | red |

3. Connect the encoder VCC and GND on the LF and RF motors (M1) on the 5V output of the step down converter (E3).
   
4. See the [front side motors layout](../schematics/front_side_motors.pdf) schematic for reference.

### 4. Connecting the back motors with the back motor driver

1. Connect the L298N back motor driver (E5) on 12V and the enable/input pins on the arduino (E4)

| L298N back motor driver (E5) | Pin on Arduino |
| ---|---:|
| ENA | D9 |
| IN1 | D25 |
| IN2 | D24 |
| IN3 | D23 |
| IN4 | D22 |
| ENB | D8 |

2. Connect the output pins of the L298N (E5) on the LB and RB motors (M1) (see the motor color table on the top of the page).

| L298N back motor driver (E5) | LB Motor (M1)|
| -----|----:|
| OUT1 | red |
| OUT2 | black |

| L298N back motor driver (E5) | RB Motor (M1)|
| -----|----:|
| OUT3 | black |
| OUT4 | red |

3. Connect the encoder VCC and GND on the LB and RB motors (M1) on the 5V output of the step down converter (E3).
   
4. See the [back side motors layout](../schematics/back_side_motors.pdf) schematic for reference.

<p float="center">
  Example wiring of the robot.
</p>

## What's next?
Congratulations! The robot wiring is complete. Follow the last part of the tutorial series to [flash the software](./../basic_circuit.md).

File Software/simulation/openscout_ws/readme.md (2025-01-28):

This is a ROS2 package for virtually simulating the OpenScout robot.

## Environment
[Ubuntu Noble 24.04.1](https://releases.ubuntu.com/noble/) 

[ROS2 Jazzy](https://docs.ros.org/en/jazzy/Installation.html)

[Gazebo Harmonic](https://gazebosim.org/docs/harmonic/ros_installation/)
 
### Further info
During the time of writing (2025), Gazebo Harmonic does not tolerate running in a virtual machine very well. It is recommended to run it on a computer with Ubuntu Noble installed natively. 

Additionally, when installing Gazebo Harmonic ensure that you do not install the standalone version. Instead first install ROS2 Jazzy, and then opt for [the version of Gazebo integrated into ROS2 Jazzy.](https://docs.ros.org/en/jazzy/Installation.html)



## Guide to running the package (On the default Ubuntu system)

First prepare the environment, as listed above.

Then make sure you have teleop twist keyboard installed.
````
sudo apt-get install ros-jazzy-teleop-twist-keyboard
````

Download or clone the repository openscout_ws, and put it in the **home** folder.

Open the Terminal and enter the following commands.

````
source /opt/ros/jazzy/setup.bash
cd ~/openscout_ws
colcon build
source install/setup.bash
ros2 launch openscout openscout.launch.py
````

This should open the simulation.

From there you can try moving the openscout with teleop keyboard.
In a new terminal enter the following:
````
source /opt/ros/jazzy/setup.bash
ros2 run teleop_twist_keyboard teleop_twist_keyboard
````

## Once in the simulation

Try driving over the slope with one side. This showcases the joint in the middle of the robot.

Feel free to make edits to the SDF to test whatever you like.

Its possible to make a python file to control the openscout using ROS2 topics.

## Example video of simulation running once set up

https://github.com/user-attachments/assets/db36529f-7577-4ad0-a52f-730f6c3506c2

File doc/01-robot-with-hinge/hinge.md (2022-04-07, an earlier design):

# Adding the hinge

The (C2.1) components have been cut using leftovers from the 3mm acrylic sheet.

Bill of materials:
| Material | Quantity | Reference | UK link |
| ---|---:|:---:|:---:|
| 200x340x3mm  acrylic sheet | 2 | C1 | [Link](https://www.acrylicsheetcuttosize.co.uk/product/clear-acrylic-sheet/) |
| Spacers from acrylic leftovers | 2 | C2.1 | [Link](https://www.acrylicsheetcuttosize.co.uk/product/clear-acrylic-sheet/) |
| Lazy Susan 5.5in | 1 | LS | [Link](https://amz.run/5TF8) |
| M4 12mm socket screw (More info needed) | 4 | S4.12 | - |
| M4 16mm socket screw (More info needed) | 4 | S4.16  | - |
| M4 Hex nuts | 8 | N1 | - |
| M5 Washers | 8 | N3 | - |

## Introduction

This tutorial includes instructions to connect the front and the back compartments using the hinge.

### Build time = 45 minutes

## Step-by-step instructions

1. TODO:
 - how to laser-cut the middle panels..
 - Upload the .dxf files in the `./cad_files` folder
 - Update the `./cad_files/README.md`

2. Fit the acrylic panel with the bigger hole in back side of the front compartment (the front and the back sides of the compartment are symmetrical), using the pre-fitted (S5.10) screws. Next, fit the acrylic panel with the smaller hole on the front side of the back compartment (the din-rail should be located on the right side of the back compartment). When tightening, ensure that diametrically apposite nuts are tightened in sequence (like you would a car wheel), to ensure even compression and reduce potential cracking.

<p float="center">
  The front compartment
  The back compartment
</p>

3. Attach the small hole of the hinge (LS) on the front compartment using the (S4.12) screws; The small hole on the hinge will help screw all of them, by rotating it to each hole.

<p float="center">
  Attaching the hinge on the front side
  Attaching the hinge on the front side
</p>

4. Insert 4 (S4.16) screws on top of 4 (N3) washers on the other side of the lazy susan (LS) and attach the spacers (C2.1) in alternating directions.

<p float="center">
  Attaching the hinge on the front side
  Attaching the hinge on the front side
</p>

5. Bring the spacers (C2.1) together forming circles and place them on top of each other in alternating directions. See the following image for reference.

<p float="center">
  Attaching the hinge on the back side
  Attaching the hinge on the back side
  Attaching the hinge on the back side
</p>

6. Finally attach the back compartment and screw the (S4.16) screws using the rest (N1) nuts. Make sure that the compartments can freely move independently.

 <p float="center">
  Attaching the hinge on the back side
</p>

## What's next?
Follow the [acrylic panels](./acrylic_panels.md) tutorial to attach the side and bottom panels on the robot.

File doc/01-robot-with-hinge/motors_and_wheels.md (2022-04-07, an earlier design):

# Motors and wheels

Bill of materials:
| Material | Quantity | Reference | UK link |
| ---|---:|:---:|:---:|
| 90:1 12V motor with encoders | 4 | M1 | [Link](https://amz.run/5TFQ) |
| Wheels (112x46mm) | 4 | M2 | [Link](shorturl.at/cwxR2) |
| Wheel Hex Driver 12mm to 17mm | 4 | M3 | [Link](shorturl.at/axT25) |
| Hex coupler 6mm | 4 | M4 | [Link](https://amz.run/5TFT) |
| Sems screw 6mm (More info needed) | 16 | P4.6 | - |
| Sems screw 8mm (More info needed) | 8 | P4.8 | - |
| M4 30mm socket screw | 4 | S4.30 | - |
| M4 Hex nuts | 12 | N1 | - |
| M4 Hammer nuts (More info needed)| 8 | N2 | - |
| M5 Washers | 8 | N3 | - |

## Introduction

We used four 12V 90:1 CQrobot motors as they provide a relatively good amount of torque and they come with encoders as well. The particular motors come with brackets, thus mounting them gets very easy.
One the other hand, the wheels selection wasn't very sophisticated, and soon they will replaced by bigger ones in order to increase ground clearence.

### Build time = 45 minutes

## Step-by-step instructions

1. Fit the motor bracket on the slots on the acrylic, by fitting in-place 2 (N2) nuts and (N3) washers using the (P4.8) screws. Ensure that the (N2) nuts are correctly secured in the channel slot. Repeat for the rest of the motors and make sure that the brackets are properly fitted by shaking them.

<p float="center">
  Attaching the motor brackets on the bottom of the chassis.
  Attaching the motor brackets on the bottom of the chassis.
  Attaching the motor brackets on the bottom of the chassis.
</p>

2. Align the (M1) motor on the bracket using the holes as a guide, and attach them using the (P4.6) screws. Repeat for the rest of the motors.

<p float="center">
  Attaching the motors on the motor brackets.
  Attaching the motors on the motor brackets.
  Attaching the motors on the motor brackets.
</p>

3. Attach the (M4) hex couplers on each motor shaft using the provided screws, and tight them. Ensure that the grub screw is tightened on the flat provided on the motor shaft. Make sure you give enough distance (~10mm) so the wheels won't touch the bracket while driving. Be sure that the hex coupler has been mounted properly by trying to pull it off.

<p float="center">
  Attaching the hex couplers on the motor brackets.
  Attaching the hex couplers on the motor brackets.
  Attaching the hex couplers on the motor brackets.
</p>

4. Attach the (M3) hex adaptors on each wheel so they can be fitted on the (M4) hex couplers. (**Optional**: If you intend driving the robot on surfaces with high friction, you can tape the wheels avoiding fast wear and tear.)

<p float="center">
  Attaching the hex adaptors on the wheels.
  Taping the wheels to avoid damaging them.
</p>

5. Fit the wheels on the shafts using the (S4.30) screws. If the screw does not fully screw on the (M4) hex coupler, use a (N1) hex nut as spacer.

<p float="center">
  Mounting the wheels on the shafts.
</p>

## What's next?
Congratulations! The robot chassis is complete. Follow the [adding the electronics](./../basic_circuit.md) tutorial to proceed with the wiring.

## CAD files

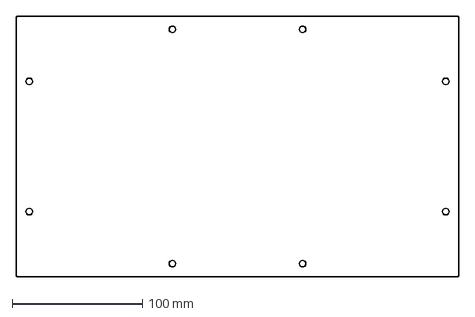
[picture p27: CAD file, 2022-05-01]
Documentation/CAD_Files/DXF/Back_back_340_200.dxf
340.0 x 200.0 mm

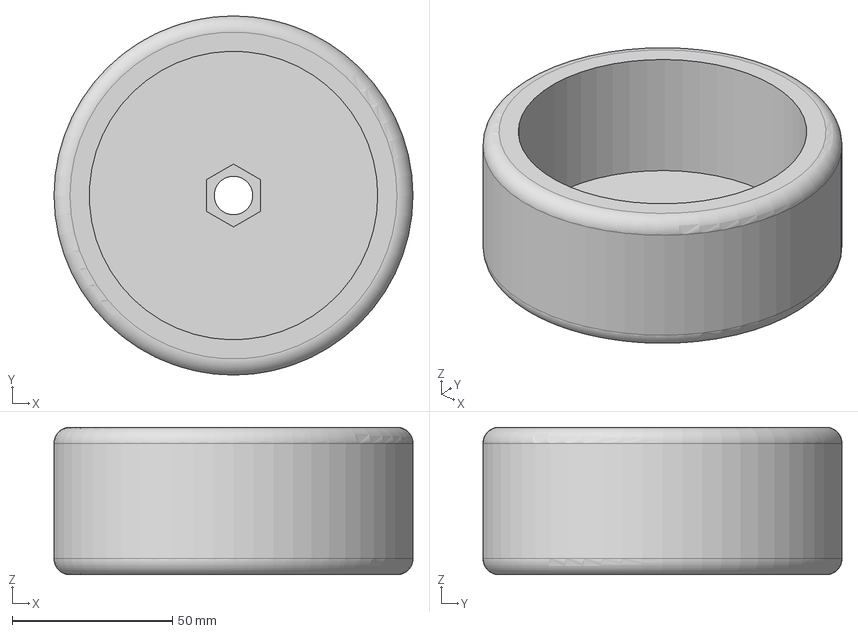
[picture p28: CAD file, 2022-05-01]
Documentation/CAD_Files/STEP/Wheel v4.step
112.0 x 112.0 x 46.0 mm

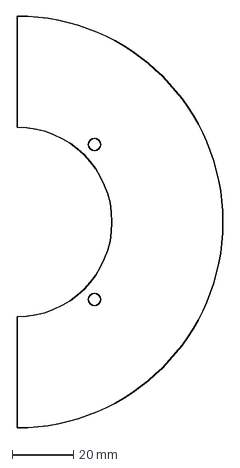
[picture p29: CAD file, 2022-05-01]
Documentation/CAD_Files/DXF/Acrylic Spacer.dxf
67.5 x 135.0 mm

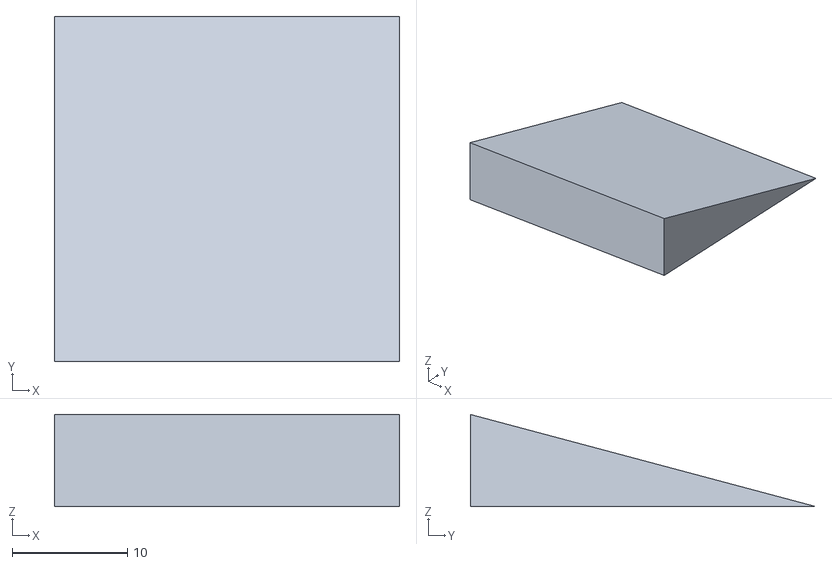
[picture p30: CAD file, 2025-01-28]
Software/simulation/openscout_ws/src/openscout/model/meshes/wedge.stl
30.0 x 30.0 x 8.00

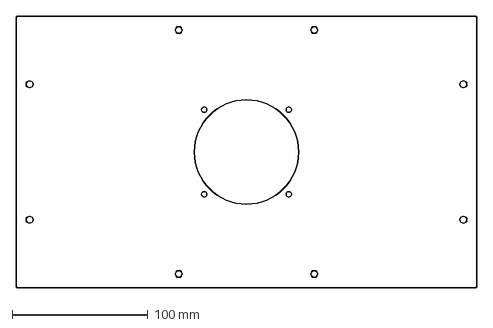
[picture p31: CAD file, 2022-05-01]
Documentation/CAD_Files/DXF/Back_middle_340_200_DXF.dxf
340.0 x 200.0 mm

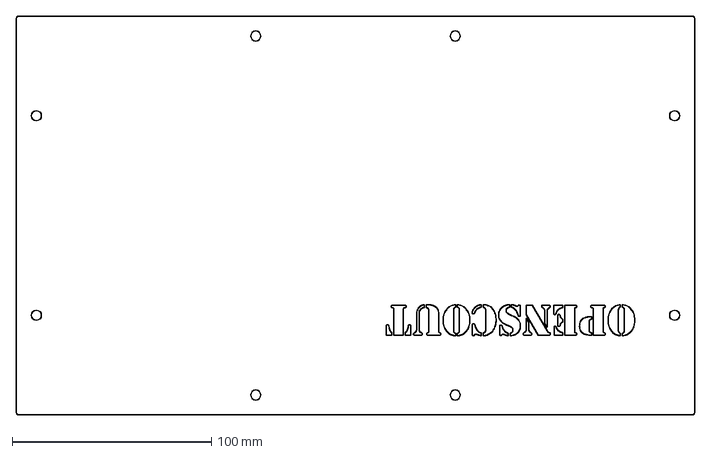
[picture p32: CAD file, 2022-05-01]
Documentation/CAD_Files/DXF/Front_Front_340_200.dxf
340.0 x 200.0 mm

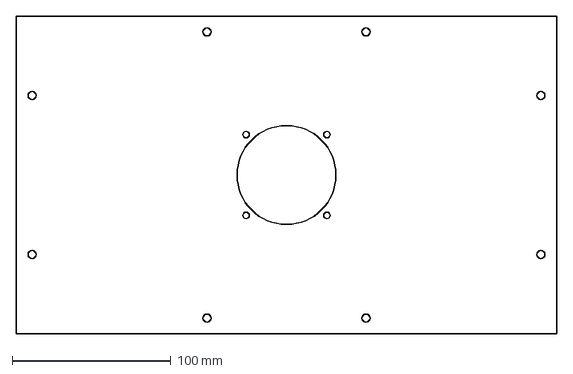
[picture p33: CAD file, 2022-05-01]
Documentation/CAD_Files/DXF/Front_middle_340_200_DXF.dxf
340.0 x 200.0 mm

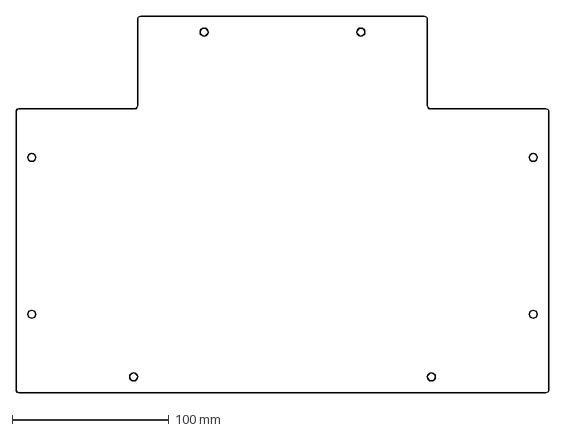
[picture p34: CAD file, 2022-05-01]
Documentation/CAD_Files/DXF/Floor_A3.dxf
340.0 x 240.0 mm

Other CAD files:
Software/simulation/openscout_ws/src/openscout/model/meshes/FrontRightWheel.stl
Software/simulation/openscout_ws/src/openscout/model/meshes/BackLeftWheel.stl
Software/simulation/openscout_ws/src/openscout/model/meshes/FrontLeftWheel.stl
Software/simulation/openscout_ws/src/openscout/model/meshes/BackRightWheel.stl

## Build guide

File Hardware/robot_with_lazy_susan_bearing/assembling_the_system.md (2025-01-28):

# 2024 Method for Assembling the System

## Step-by-step instructions

### Step 1

<p float="center">
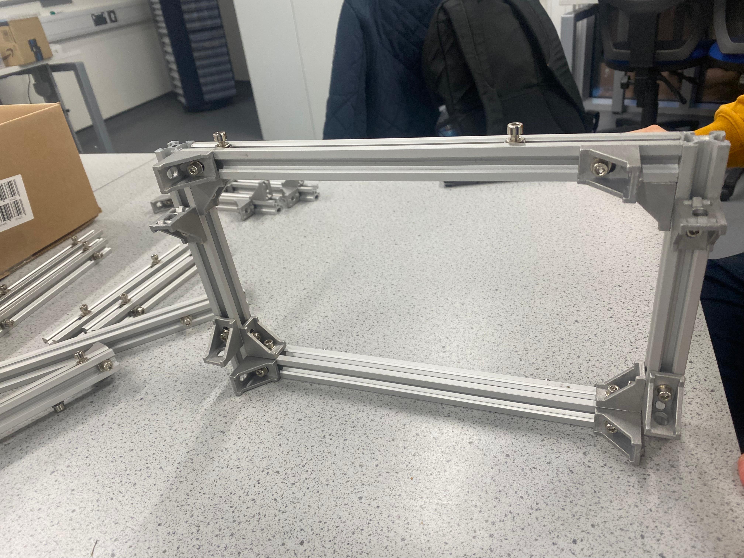
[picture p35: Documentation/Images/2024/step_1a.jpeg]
  
</p>

<p float="center">
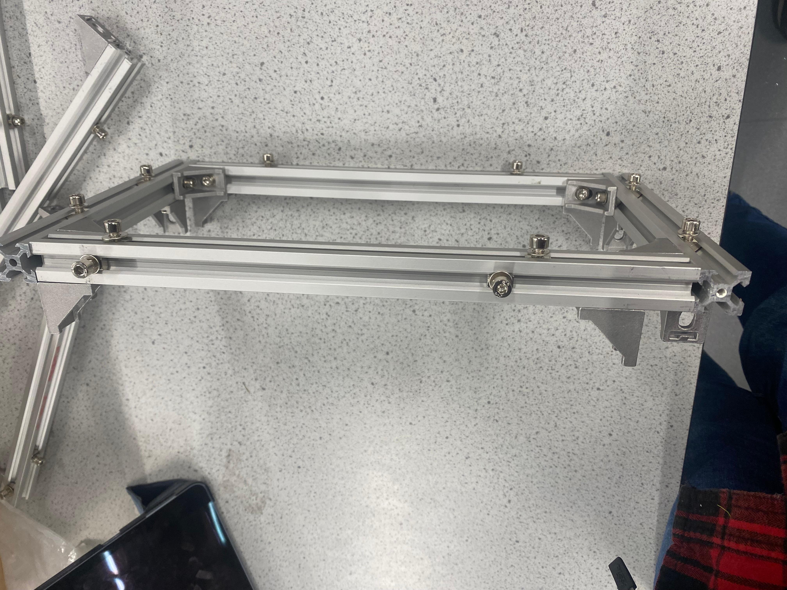
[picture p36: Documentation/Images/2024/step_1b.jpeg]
  
</p>

<p float="center">
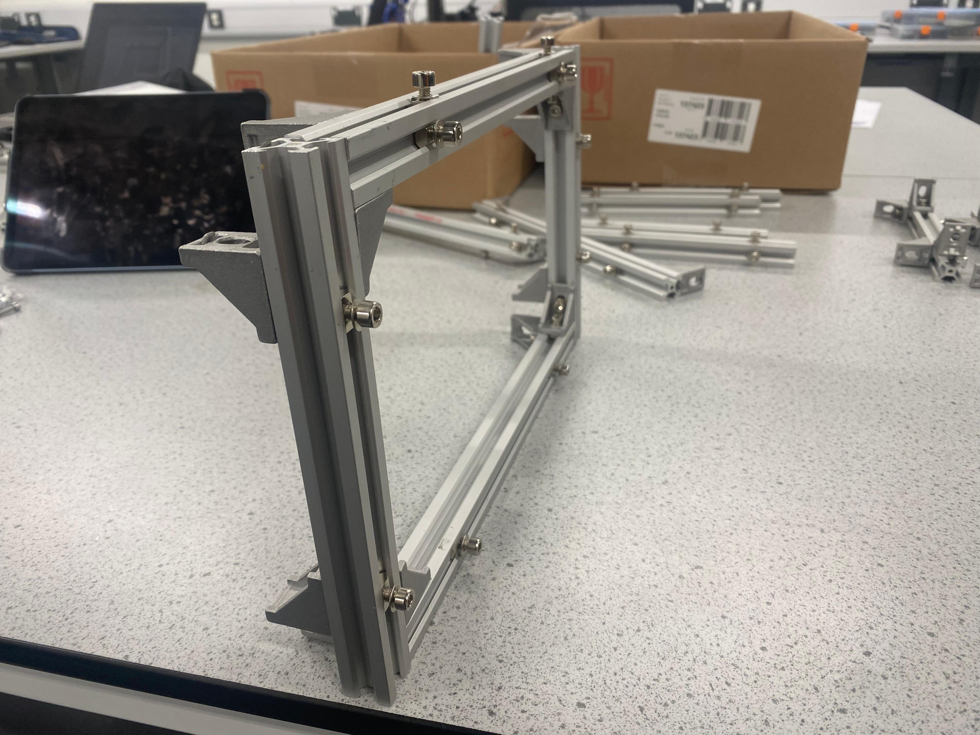
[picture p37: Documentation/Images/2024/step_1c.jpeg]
  
</p>

<p float="center">
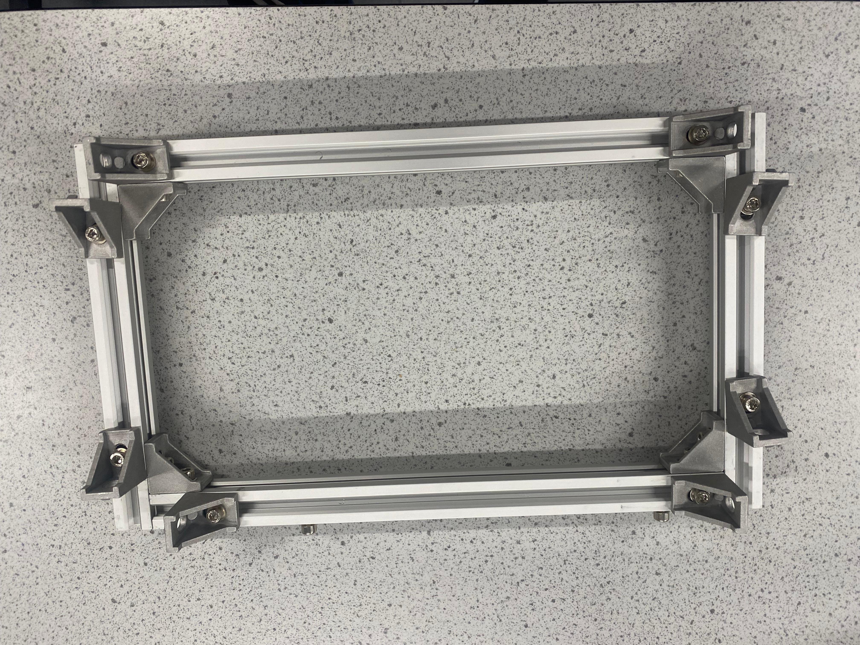
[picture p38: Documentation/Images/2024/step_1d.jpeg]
  
</p>

### Step 2

<p float="center">
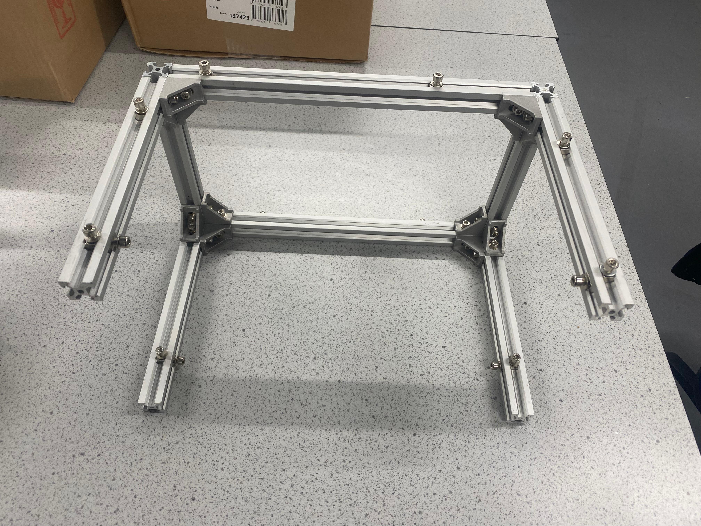
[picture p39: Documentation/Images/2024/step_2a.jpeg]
  
</p>

<p float="center">
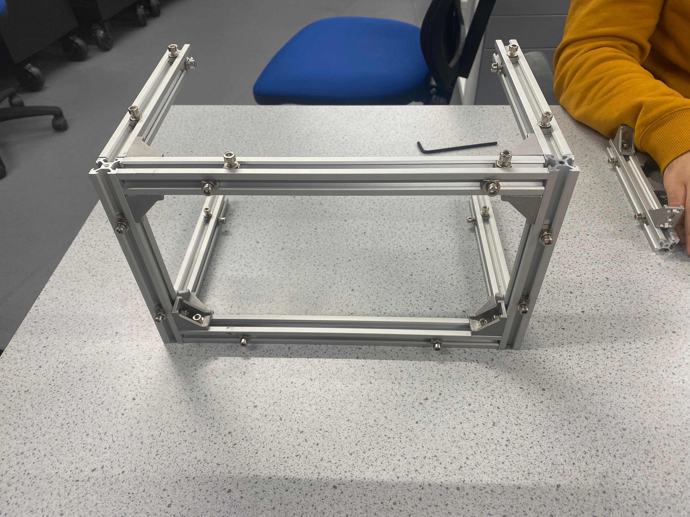
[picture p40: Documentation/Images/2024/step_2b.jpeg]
  
</p>

<p float="center">
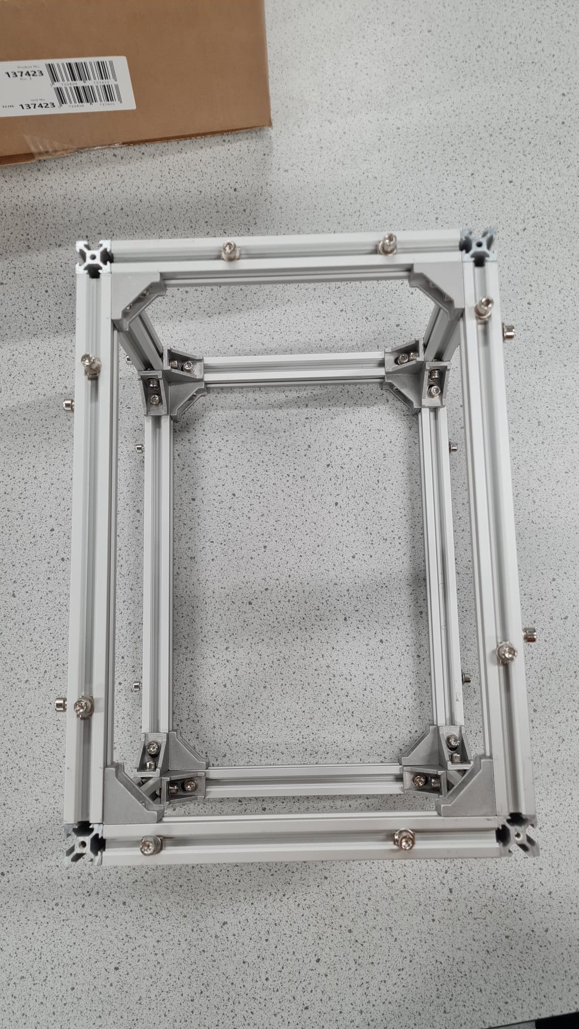
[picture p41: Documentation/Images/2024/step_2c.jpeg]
  
</p>

### Step 3

<p float="center">
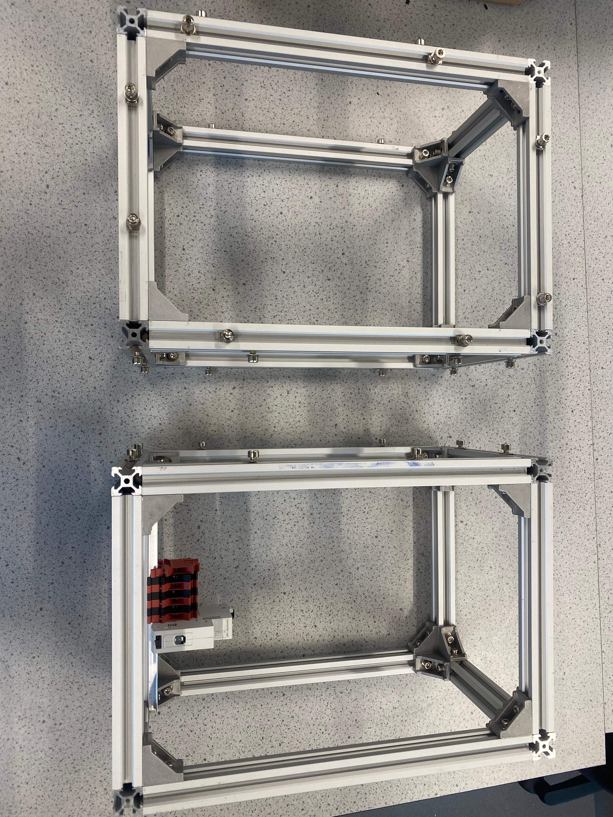
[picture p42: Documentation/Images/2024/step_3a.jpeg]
  
</p>

<p float="center">
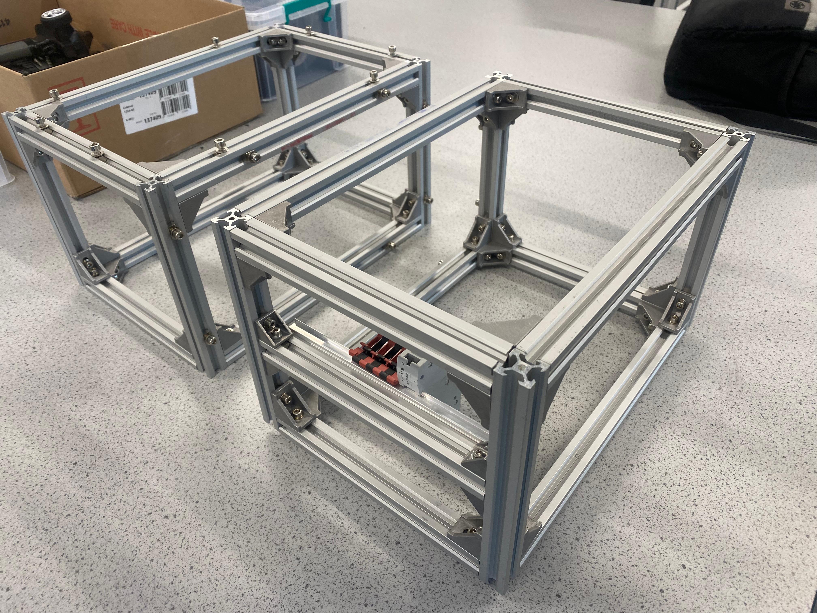
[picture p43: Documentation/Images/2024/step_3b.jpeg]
  
</p>

<p float="center">
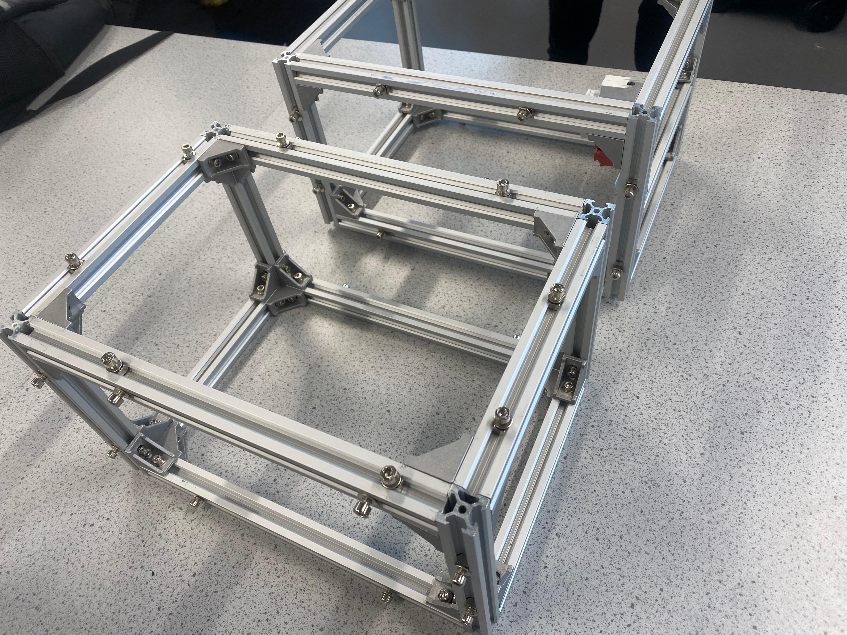
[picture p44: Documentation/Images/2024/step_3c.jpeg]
  
</p>

<p float="center">
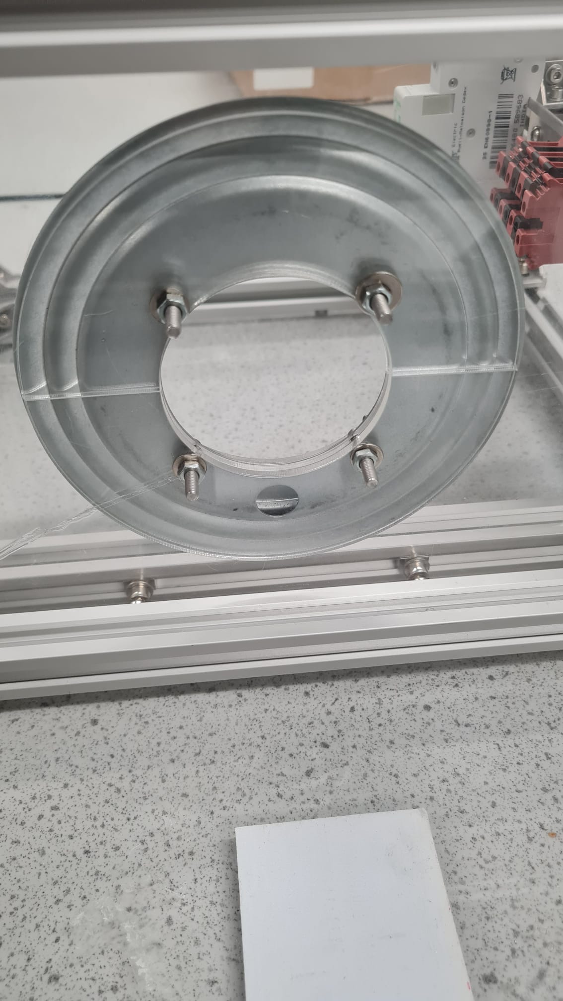
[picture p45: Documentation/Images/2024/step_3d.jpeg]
  
</p>

### Step 4

<p float="center">
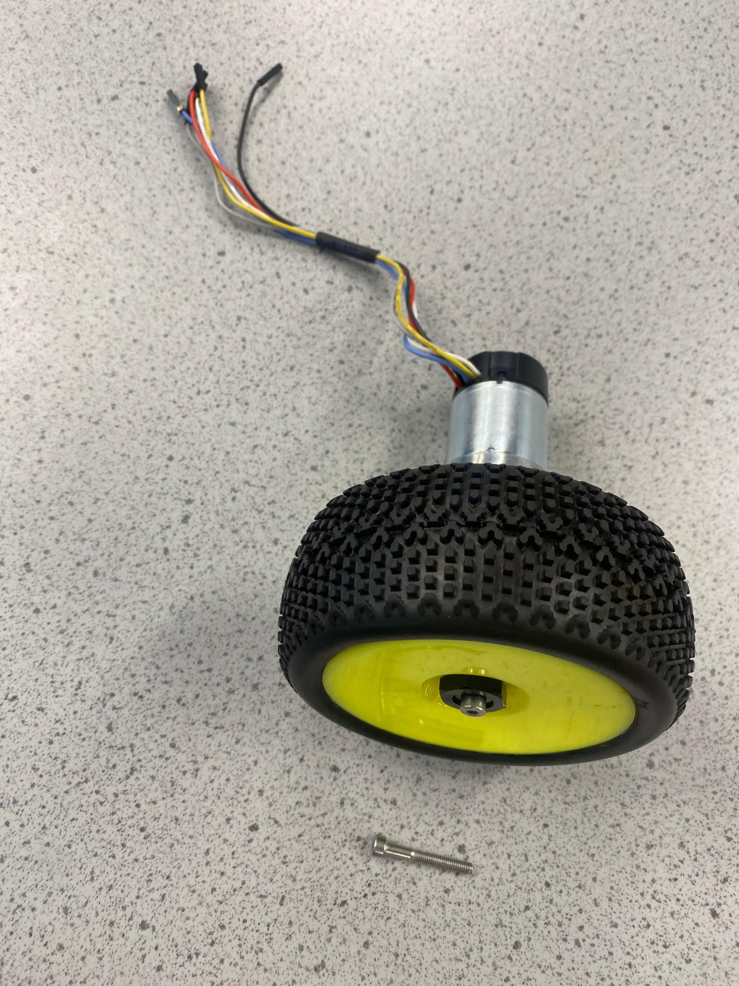
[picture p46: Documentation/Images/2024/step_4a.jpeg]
  
</p>

<p float="center">
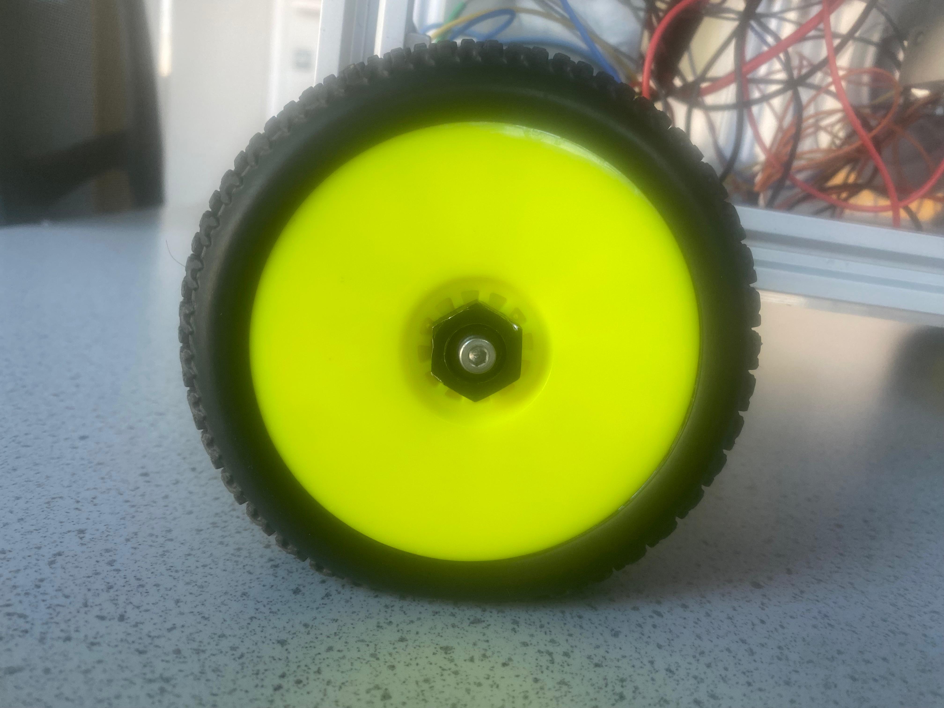
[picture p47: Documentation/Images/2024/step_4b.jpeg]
  
</p>

### Step 5

<p float="center">
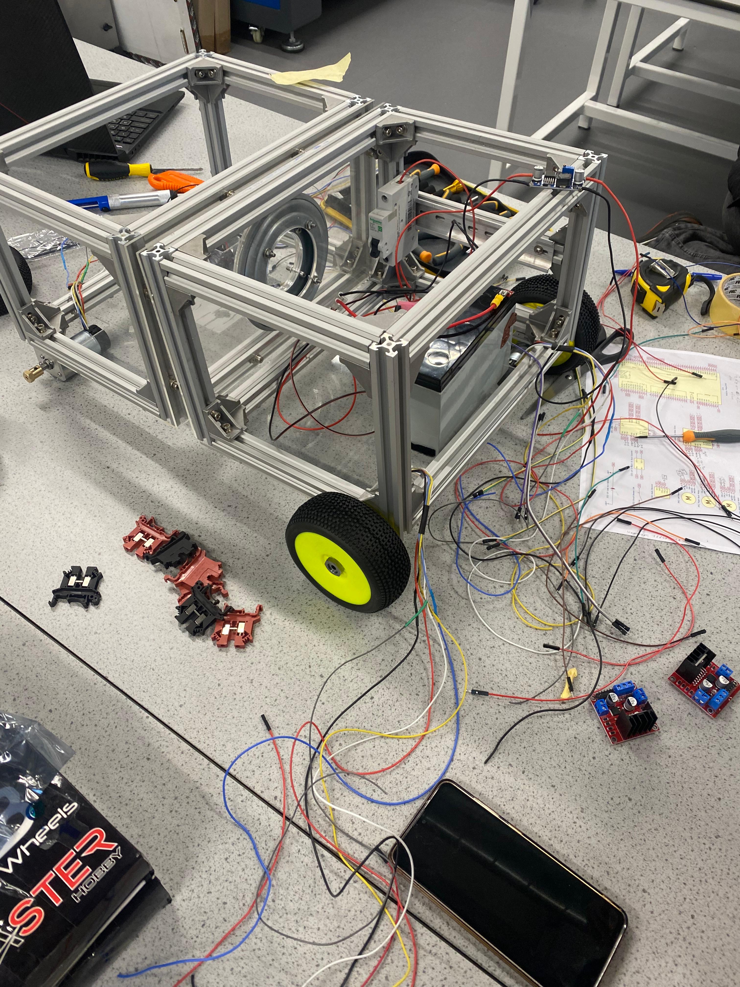
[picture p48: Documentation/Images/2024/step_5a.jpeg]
  
</p>

<p float="center">
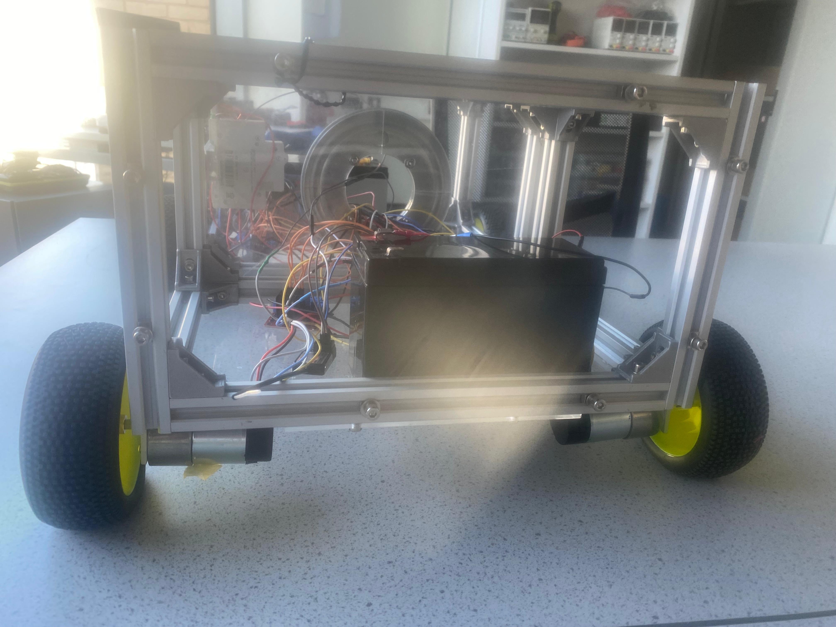
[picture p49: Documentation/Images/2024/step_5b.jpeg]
  
</p>

<p float="center">
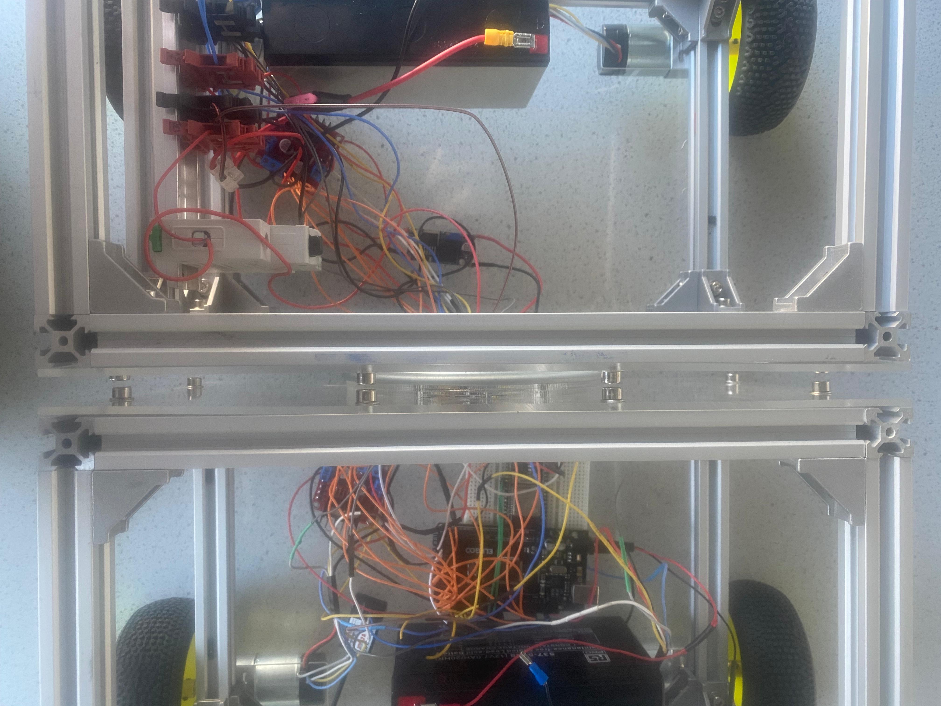
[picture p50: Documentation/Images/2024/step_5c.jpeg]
  
</p>

<p float="center">
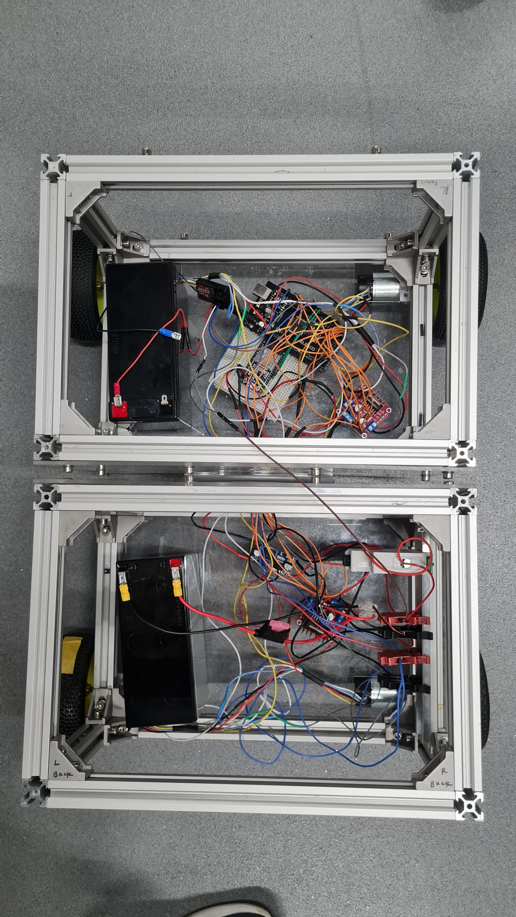
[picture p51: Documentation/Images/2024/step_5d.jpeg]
  
</p>

## Wiring Diagram

1. See the [Simplified System Schematic](../../Documentation/Schematics/simplified_system_layout_2024.pdf) schematic for reference.

<p float="center">
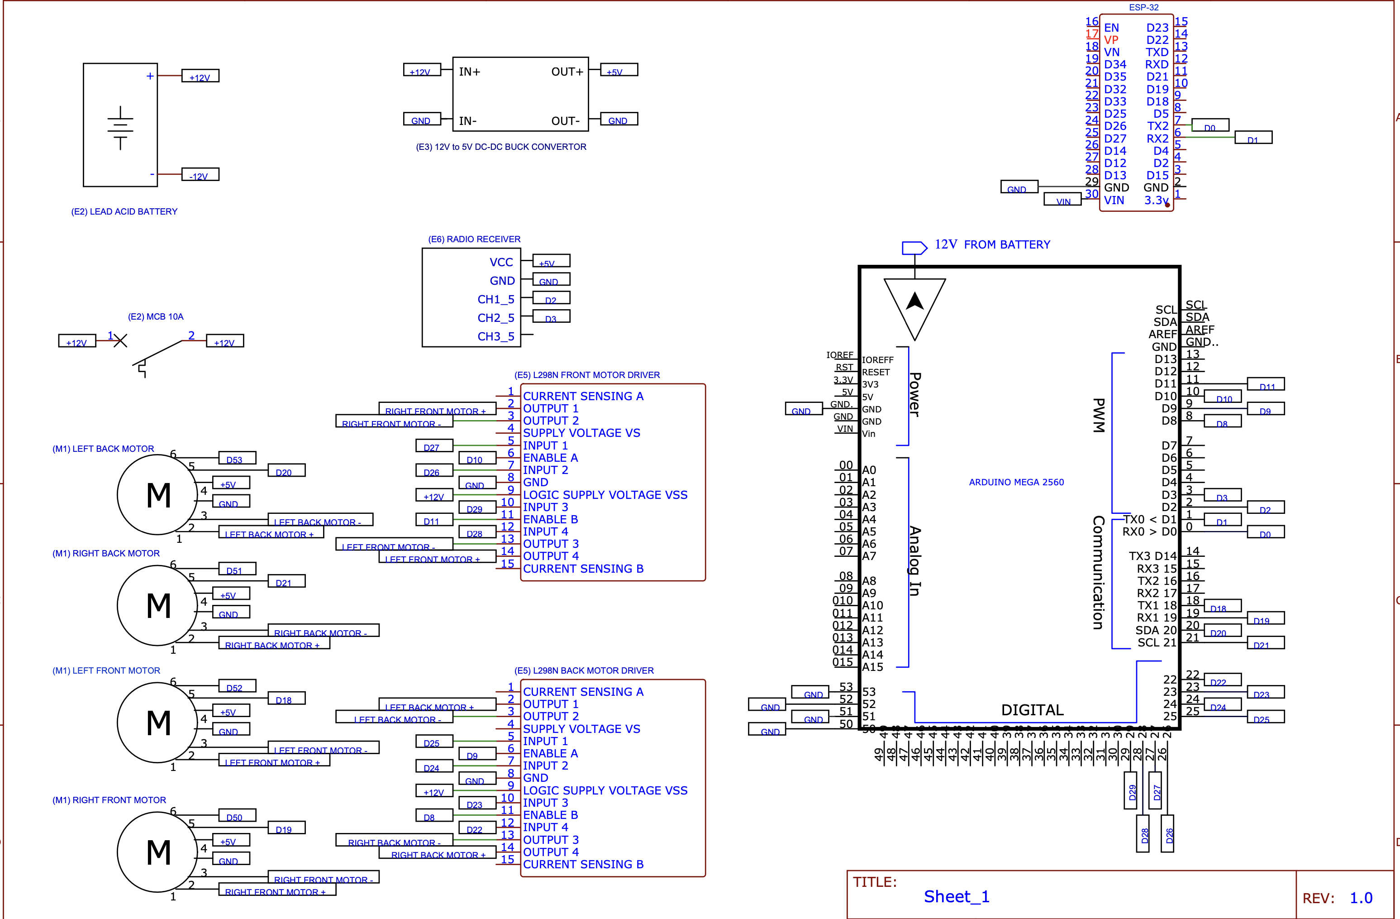
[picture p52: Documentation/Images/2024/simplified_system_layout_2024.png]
Simplified System Schematic
  
</p>

2. See the [Full System Schematic](../../Documentation/Schematics/full_system_layout_2024.pdf) schematic for reference.

<p float="center">
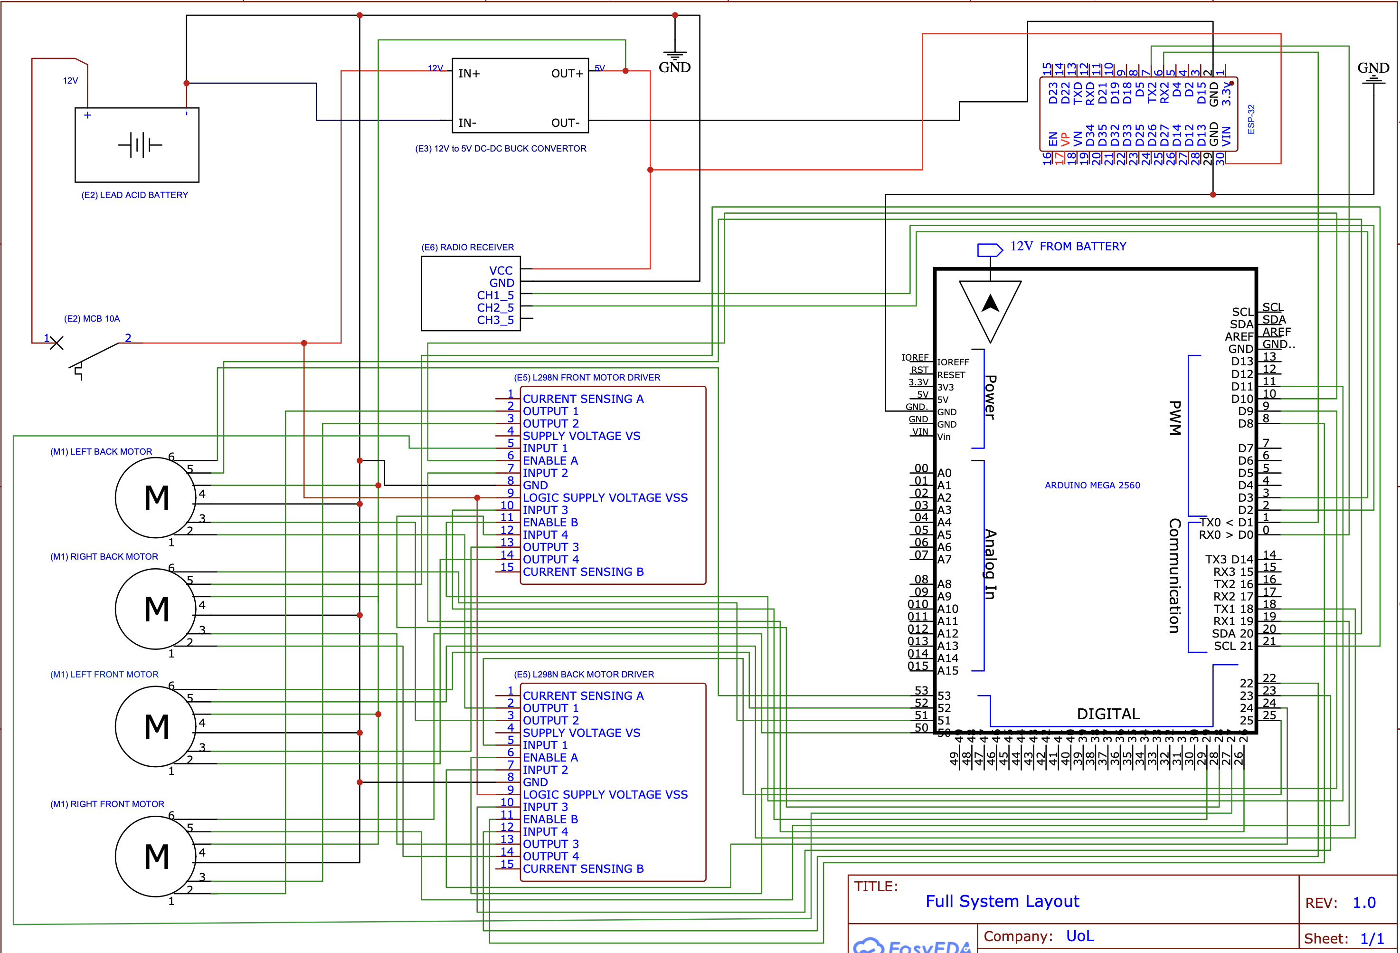
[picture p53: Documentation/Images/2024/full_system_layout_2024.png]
Full System Schematic
  
</p>

## OpenScout driving

https://github.com/user-attachments/assets/b3fbb942-297d-4cb1-b123-8d51ed27b225

## What's next?
Congratulations! The robot wiring is complete. Follow the last part of the tutorial series to [flash the software](../../Software/README.md).

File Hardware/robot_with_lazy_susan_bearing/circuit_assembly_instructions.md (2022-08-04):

# Electronics layout

## Build time = 75 minutes

### Bill of materials:

| Material | Quantity | Reference | UK link |
| ---|---:|:---:|:---:|
| 12V Lead Acid battery | 1 | E1 | [Link](https://uk.rs-online.com/web/p/lead-acid-batteries/0597835) |
| 10A circuit breaker | 1 | E2 | [Link](https://amz.run/5TFI) |
| Buck converter | 1 | E3 | [Link](https://amz.run/5TFJ) |
| Arduino Mega | 1 | E4 | [Link](https://amz.run/5TFL) |
| L298N Motor drivers | 2 | E5 | [Link](https://amz.run/5TFN) |
| Radio transmitter-receiver | 1 | E6 | [Link](https://amz.run/5TFO) |
| 90:1 12V motor with encoders | 4 | M1 | [Link](https://amz.run/5TFQ) |
| Din rail with terminal blocks | 1 | DT | [Link](https://amz.run/5TFF) |
| Velcro 50mmx1m | 1 | Q | [Link](https://amz.run/5TFP) |
| Breadboards | - | - | - |
| Wires | - | - | - |

CQrobot Motor (M1) pinout:
| Motor (M1) | wire |
| ---|-----:|
| ENC_A  | yellow |
| ENC_B  | white |
| VCC | blue |
| GND | gray |
| MOTOR+ | red |
| MOTOR- | black |

## Introduction

This tutorial provides instructions for wiring together the electronic components. Example photos are provided and can be used as reference, however some of the components are optional (e.g. the terminal blocks (DT) on the din rail, and the breadboards) but you are free to replace them with other components such as veroboards, depending on your soldering experience. The schematics provided in `.pdf` format show in-detail how the different components are connected together. (**WARNING**: Please handle the Lead Acid battery (E1) with care.)

## Wiring Diagram

<p float="center">
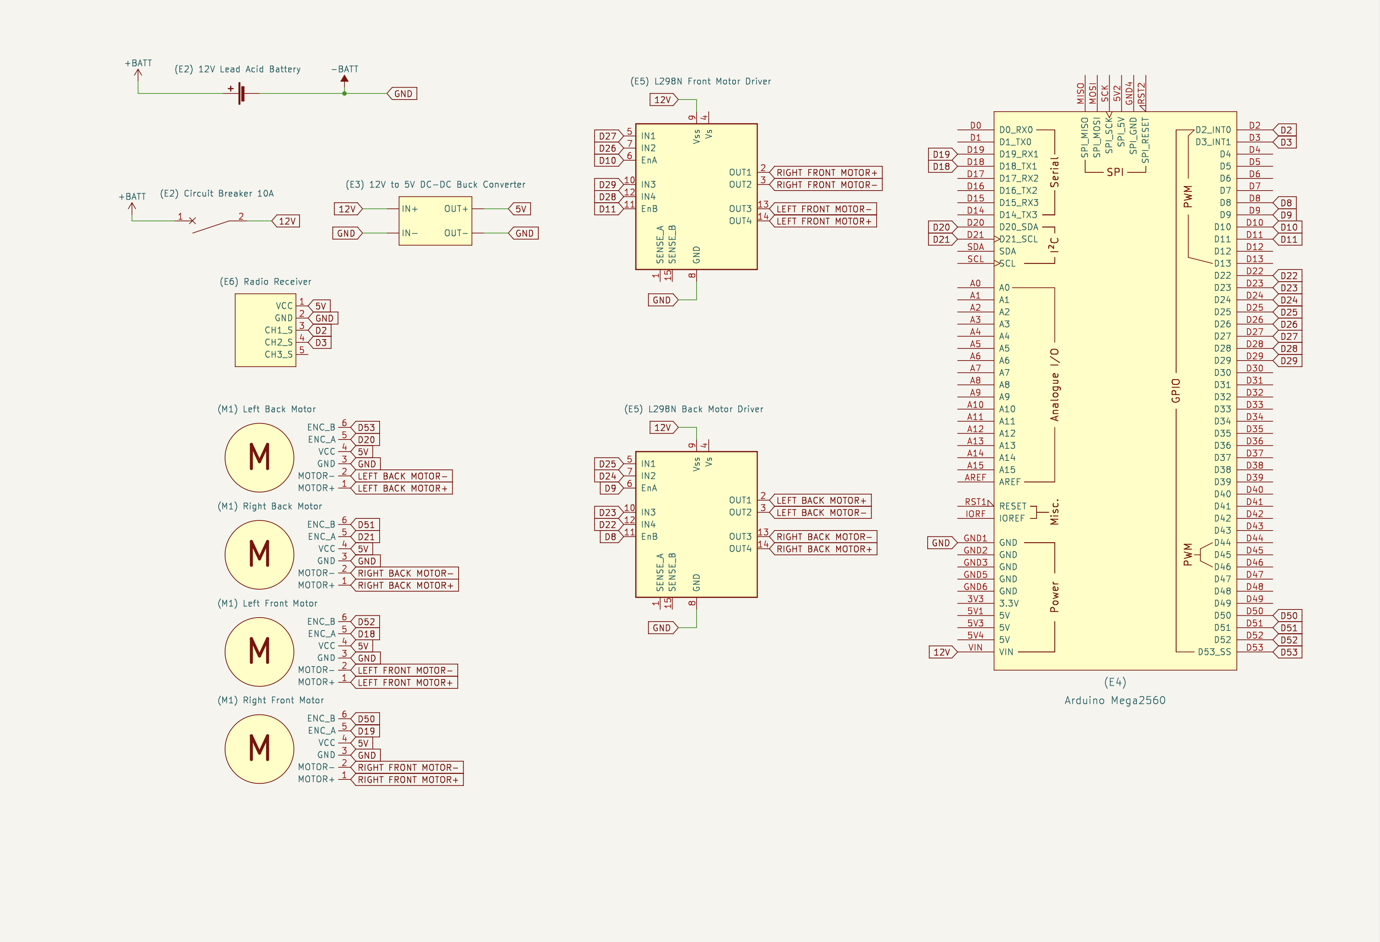
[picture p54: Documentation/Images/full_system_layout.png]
Wiring diagram.
  
</p>

## Step-by-step instructions

### 1. Connecting the arduino

1. Attach a strap of velcro (Q) either on the back or the front of the robot (depending on where you'd like to place the battery), and on the bottom of the battery (E1) so you can secure it on the robot. You can use the terminal blocks on the din rail (DT) to prepare some 12V and 5V (using the step down converter (E3)) power lines to power the components.

2. See the [arduino layout](../../Documentation/Schematics/arduino_layout.pdf) schematic for reference.

<p float="center">
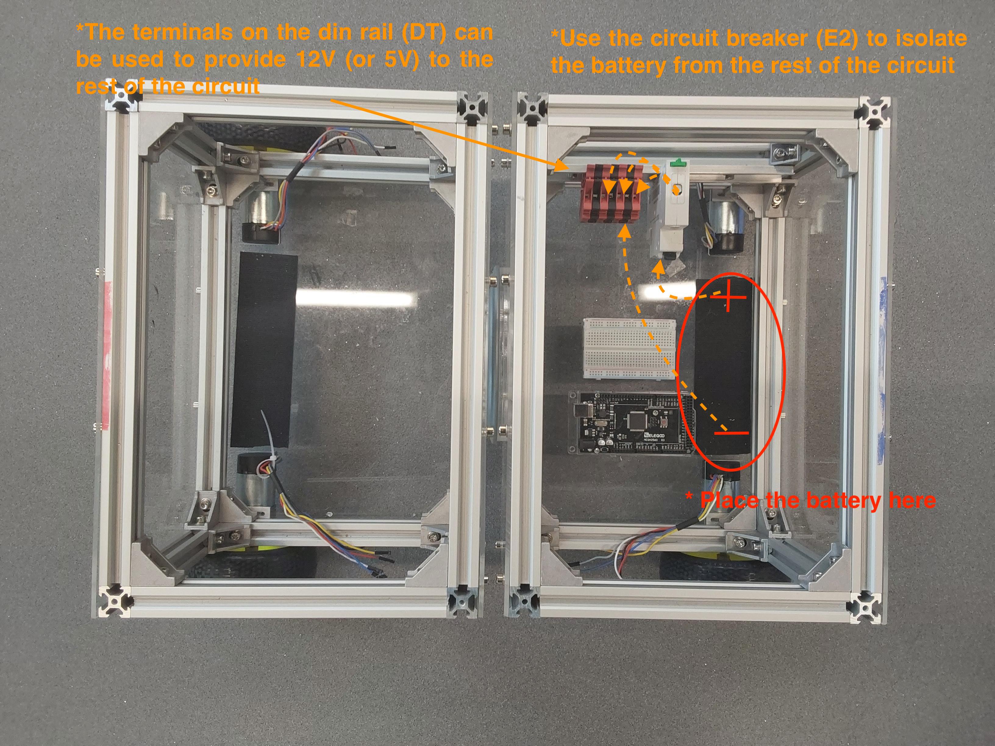
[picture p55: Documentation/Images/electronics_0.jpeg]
Attaching the motor brackets on the bottom of the chassis.
  
</p>

### 2. Attaching the radio receiver

1. Power the radio receiver (E6) using 5V from the step down converter (E3)
2. Connect the ground from the radio receiver (E6)
3. Connect radio receiver (E6) channels on the arduino (E4) as follows:

| radio receiver (E6) | Pin on Arduino |
| ---|---:|
| CH1_S | D2 |
| CH2_S | D3 |

<p float="center">
  Connecting the radio receiver.
</p>

4. See the [radio receiver layout](../../Documentation/Schematics/rc_layout.pdf) schematic for reference.

### 3. Connecting the front motors with the front motor driver

1. Connect the L298N front motor driver (E5) on 12V and the enable/input pins on the arduino (E4)

| L298N front motor driver (E5) | Pin on Arduino |
| ---|---:|
| ENA | D10 |
| IN1 | D27 |
| IN2 | D26 |
| IN3 | D29 |
| IN4 | D28 |
| ENB | D11 |

2. Connect the output pins of the L298N (E5) on the LF and RF motors (M1) (see the motor color table on the top of the page).

| L298N front motor driver (E5) | RF Motor (M1)|
| -----|----:|
| OUT1 | red |
| OUT2 | black |

| L298N front motor driver (E5) | LF Motor (M1)|
| -----|----:|
| OUT3 | black |
| OUT4 | red |

3. Connect the encoder VCC and GND on the LF and RF motors (M1) on the 5V output of the step down converter (E3).
   
4. See the [front side motors layout](../../Documentation/Schematics/front_side_motors.pdf) schematic for reference.

### 4. Connecting the back motors with the back motor driver

1. Connect the L298N back motor driver (E5) on 12V and the enable/input pins on the arduino (E4)

| L298N back motor driver (E5) | Pin on Arduino |
| ---|---:|
| ENA | D9 |
| IN1 | D25 |
| IN2 | D24 |
| IN3 | D23 |
| IN4 | D22 |
| ENB | D8 |

2. Connect the output pins of the L298N (E5) on the LB and RB motors (M1) (see the motor color table on the top of the page).

| L298N back motor driver (E5) | LB Motor (M1)|
| -----|----:|
| OUT1 | red |
| OUT2 | black |

| L298N back motor driver (E5) | RB Motor (M1)|
| -----|----:|
| OUT3 | black |
| OUT4 | red |

3. Connect the encoder VCC and GND on the LB and RB motors (M1) on the 5V output of the step down converter (E3).
   
4. See the [back side motors layout](../../Documentation/Schematics/back_side_motors.pdf) schematic for reference.

<p float="center">
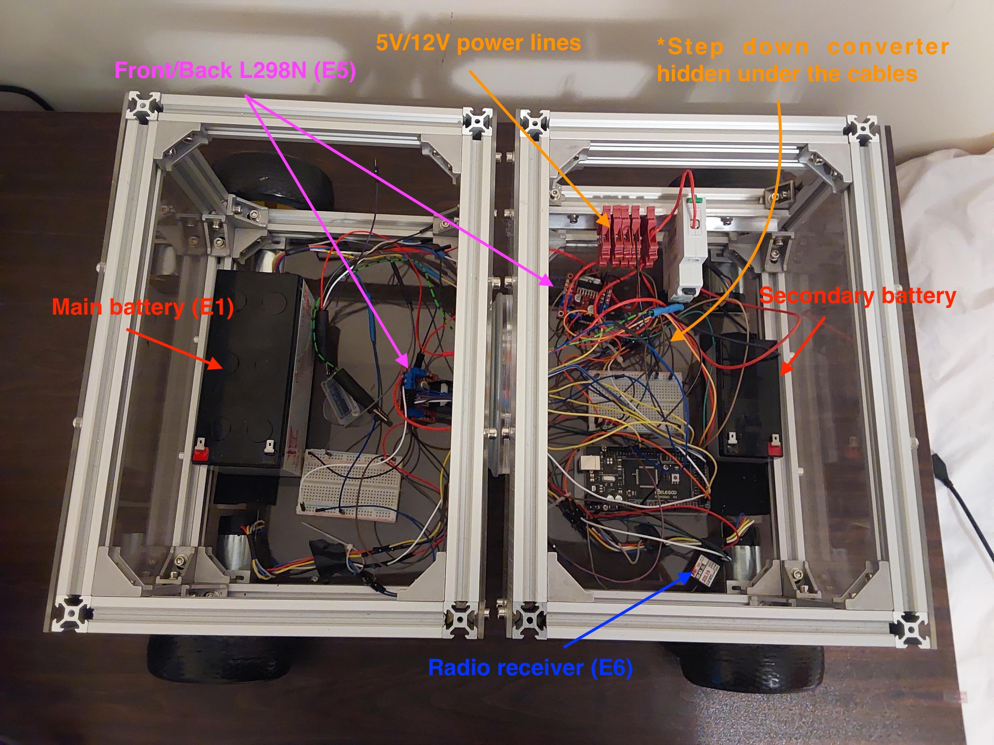
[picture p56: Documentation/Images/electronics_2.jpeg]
Example wiring of the robot.
  
</p>

## What's next?
Congratulations! The robot wiring is complete. Follow the last part of the tutorial series to [flash the software](../../Software/README.md).

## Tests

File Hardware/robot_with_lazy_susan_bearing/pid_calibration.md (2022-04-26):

# Speed PID controller calibration

## Calibration time = 20 minutes

The robot drives using [differential robot kinematics](https://www.cs.columbia.edu/~allen/F19/NOTES/icckinematics.pdf). We use PID controller to set the desired speed (linear and angular) which is then converted in rad/s. To tune the PID controller, all three gain values are initially set to zero and then tuned independently by comparing the actual and the desired motor speed in the Arduino IDE's serial plotter (To open the serial plotter in the IDE `Tools -> Serial Plotter`).

1. Firstly, the motors’ speed is set in a square wave between 1/3 and 2/3 of the maximum speed (in rad/s). The maximum speed does not need to be found, rather than getting a rough estimation of it. The rationale behind the `[1/3,2/3]` speed interval is to produce a speed flunctuation, but the actual values can be arbitrary. 
2. `Kp` is gradually increased until motors reach the desired speed in the Serial Plotter. Notice that the actual speed will never reach the set speed. A good `Kp` good value is chosen when the actual speed is slightly less than the desired speed. 
3. Next, `Ki` is gradually increased so that the motors speed converges to the desired speed. Oscillations around the setpoint will occur from overshooting. At this point, the motors can reach and oscillate around the desired speed. Increase the $Ki$ until you observe a slight oscillation around the desired speed.
4. To reduce overshoooting, gradually increase `Kd` until the oscillations around the setpoint are removed.

In our implemenation we found `Kp=2, Ki=5, Kd=1` as optimal.

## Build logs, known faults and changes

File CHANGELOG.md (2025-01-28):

# Changelog

All notable changes to this project will be documented in this file.

## Contributors

The names listed in the image are:
- Robbie Cato
- Bartosz Krawczyk
- Ahmed Elbary
- Nivetha Sakthivel
- Kaung Myat
- Jagdish Patil
- Anyeh Ndi-Tah

## [23/01/2025] - Feature Changes

See Demonstrations folder for more videos.

### Attempted to replace Arduino with ESP32
- It was found to not have enough pins, therefore used Arduino ATMEGA and ESP32.
- ATMEGA controls motors and motor drivers.
- ESP32 receives MQTT messages, and translates them into motor control commands.

### Battery adjustments
- Increased the capacity of the secondary battery (that powers the Arduino ATMEGA and ESP32).

### Control software
- MQTT communication and Twist to JSON code has been tested by modulating LED intensities to prove core concept.
- For use with an ATMEGA, a WiFi shield was needed for testing on OpenScout. Works well with the ESP32 but lacks enough pins to control the robot.
- Implemented radio receiver which converts radio commands into throttle and angular values instead.
- Replaced `simple_pid.ino` with `refined_pid.ino`.

### Added simulation software
- A simulated version of the OpenScout was created.
- Implemented using Gazebo Harmonic and ROS2.

### Changes to documentation
- Updated demonstrations with changes.

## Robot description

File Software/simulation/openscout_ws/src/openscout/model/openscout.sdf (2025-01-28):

<?xml version="1.0" ?>
<sdf version="1.6">
    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 
    <world name="openscout">
        
        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
        <physics name="1ms" type="ignored">
            <max_step_size>0.01</max_step_size>
            <real_time_factor>1</real_time_factor>
        </physics>

        <plugin filename="gz-sim-physics-system" name="gz::sim::systems::Physics">
        </plugin>

        <plugin filename="gz-sim-user-commands-system" name="gz::sim::systems::UserCommands">
        </plugin>

        <plugin filename="gz-sim-scene-broadcaster-system" name="gz::sim::systems::SceneBroadcaster">
        </plugin>
        
        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
        <light type="directional" name="sun">
            <cast_shadows>true</cast_shadows>
            <pose>0 0 10 0 0 0</pose>
            <diffuse>0.8 0.8 0.8 1</diffuse>
            <specular>0.2 0.2 0.2 1</specular>
            <attenuation>
                <range>1000</range>
                <constant>0.9</constant>
                <linear>0.01</linear>
                <quadratic>0.001</quadratic>
            </attenuation>
            <direction>-0.5 0.1 -0.9</direction>
        </light>

        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
        <model name="ground_plane">
            <static>true</static>
            <link name="link">
                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
            </link>
        </model>
        
        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
        <model name='open_scout' canonical_link='front_chassis'>
            <pose relative_to='world'>0 0 0.5 0 0 0</pose>

            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
            <link name='front_chassis'>
                <pose relative_to='__model__'>0 0 -0.05 0 0 0</pose>
                <inertial>
                    <mass>3.5</mass>
                    <inertia>
                        <ixx>0.0233</ixx>
                        <ixy>0</ixy>
                        <ixz>0</ixz>
                        <iyy>0.0379</iyy>
                        <iyz>0</iyz>
                        <izz>0.0379</izz>
                    </inertia>
                </inertial>
                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
            </link>
            
            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
            <link name='back_chassis'>
                <pose relative_to='front_chassis'>0 0 0 0 0 0</pose>
                <inertial>
                    <mass>5.5</mass>
                        <inertia>
                            <ixx>0.03667</ixx>
                            <ixy>0.0</ixy>
                            <ixz>0.0</ixz>
                            <iyy>0.05958</iyy>
                            <iyz>0.0</iyz>
                            <izz>0.05958</izz>
                        </inertia>
                </inertial>

                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
            </link>


            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
            <joint name='lazy_susan_joint' type='revolute'>
                <parent>front_chassis</parent>
                <child>back_chassis</child>
                <pose relative_to='front_chassis'>0 0 0 0 0 0</pose>
                <axis>
                    <xyz>0 1 0</xyz> 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
                </axis>
            </joint>

            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
            <link name='front_right_wheel'>
                <pose relative_to="front_chassis">0 0 0 0 0 0</pose>
                <inertial>
                    <mass>0.150</mass>
                    <inertia>
                        <ixx>0.000361275</ixx>
                        <ixy>0</ixy>
                        <ixz>0</ixz>
                        <iyy>0.000361275</iyy>
                        <iyz>0</iyz>
                        <izz>0.000361275</izz>
                    </inertia>
                </inertial>
                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
            </link>

            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
            <link name='front_left_wheel'>
                <pose relative_to="front_chassis">0 0 0 0 0 0</pose>
                <inertial>
                    <mass>0.150</mass>
                    <inertia>
                        <ixx>0.000361275</ixx>
                        <ixy>0</ixy>
                        <ixz>0</ixz>
                        <iyy>0.000361275</iyy>
                        <iyz>0</iyz>
                        <izz>0.000361275</izz>
                    </inertia>
                </inertial>
                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
            </link>

            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
            <link name='back_right_wheel'>
                <pose relative_to="back_chassis">0 0 0 0 0 0</pose>
                <inertial>
                    <mass>0.150</mass>
                    <inertia>
                        <ixx>0.000361275</ixx>
                        <ixy>0</ixy>
                        <ixz>0</ixz>
                        <iyy>0.000361275</iyy>
                        <iyz>0</iyz>
                        <izz>0.000361275</izz>
                    </inertia>
                </inertial>
                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
            </link>

            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
            <link name='back_left_wheel'>
                <pose relative_to="back_chassis">0 0 0 0 0 0</pose>
                <inertial>
                    <mass>0.150</mass>
                    <inertia>
                        <ixx>0.000361275</ixx>
                        <ixy>0</ixy>
                        <ixz>0</ixz>
                        <iyy>0.000361275</iyy>
                        <iyz>0</iyz>
                        <izz>0.000361275</izz>
                    </inertia>
                </inertial>
                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
            </link>

            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
            <joint name="front_right_wheel_joint" type="revolute">
                <pose>-0.2 -0.19 -0.03 0 1.5708 0</pose>
                <parent>front_chassis</parent>
                <child>front_right_wheel</child>
                <axis>
                    <xyz expressed_in='__model__'>1 0 0</xyz>
                    <limit>
                        <lower>-1.79769e+308</lower>
                        <upper>1.79769e+308</upper>
                    </limit>
                </axis>
            </joint>
            
            <joint name="front_left_wheel_joint" type="revolute">
                <pose>0.2 -0.19 -0.03 0 1.5708 0</pose>
                <parent>front_chassis</parent> 
                <child>front_left_wheel</child>
                <axis>
                    <xyz expressed_in='__model__'>1 0 0</xyz>
                    <limit>
                        <lower>-1.79769e+308</lower>
                        <upper>1.79769e+308</upper>
                    </limit>
                </axis>
            </joint>

            <joint name="back_right_wheel_joint" type="revolute">
                <pose>-0.2 0.23 -0.03 0 1.5708 0</pose>
                <parent>back_chassis</parent>
                <child>back_right_wheel</child>
                <axis>
                    <xyz expressed_in='__model__'>1 0 0</xyz>
                    <limit>
                        <lower>-1.79769e+308</lower>
                        <upper>1.79769e+308</upper>
                    </limit>
                </axis>
            </joint>
            
            <joint name="back_left_wheel_joint" type="revolute">
                <pose>0.2 0.23 -0.03 0 1.5708 0</pose>
                <parent>back_chassis</parent>
                <child>back_left_wheel</child>
                <axis>
                    <xyz expressed_in='__model__'>1 0 0</xyz>
                    <limit>
                        <lower>-1.79769e+308</lower>
                        <upper>1.79769e+308</upper>
                    </limit>
                </axis>
            </joint>

            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
            <plugin filename="gz-sim-diff-drive-system" name="gz::sim::systems::DiffDrive">
                <left_joint>front_left_wheel_joint</left_joint>
                <left_joint>back_left_wheel_joint</left_joint>
                <right_joint>front_right_wheel_joint</right_joint>
                <right_joint>back_right_wheel_joint</right_joint>
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

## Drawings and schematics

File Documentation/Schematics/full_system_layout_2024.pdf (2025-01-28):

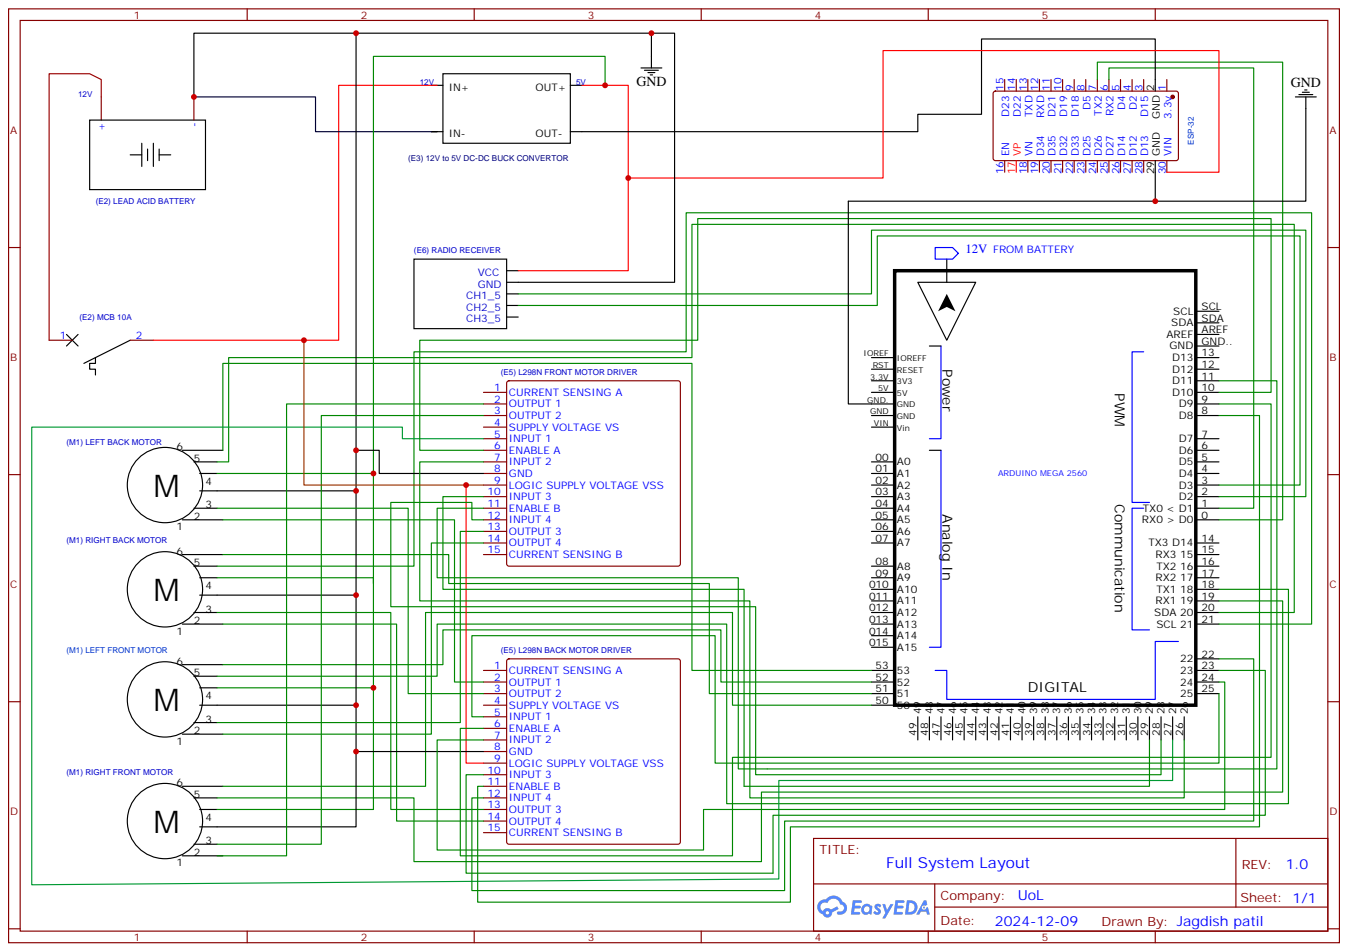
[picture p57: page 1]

3.3v 1 GND 2 D15 3 D2 4 D4 5 RX2 6 TX2 7 D5 8 D18 9 D19 10 D21 11 RXD 12 TXD 13 D22 14 D23 15 EN 16 VP 17 VN 18 D34 19 D35 20 D32 21 D33 22 D25 23 D26 24 D27 25 D14 26 D12 27 D13 28 GND 29 VIN 30

(E3) 12V to 5V DC-DC BUCK CONVERTOR

Drawn By: Jagdish patil

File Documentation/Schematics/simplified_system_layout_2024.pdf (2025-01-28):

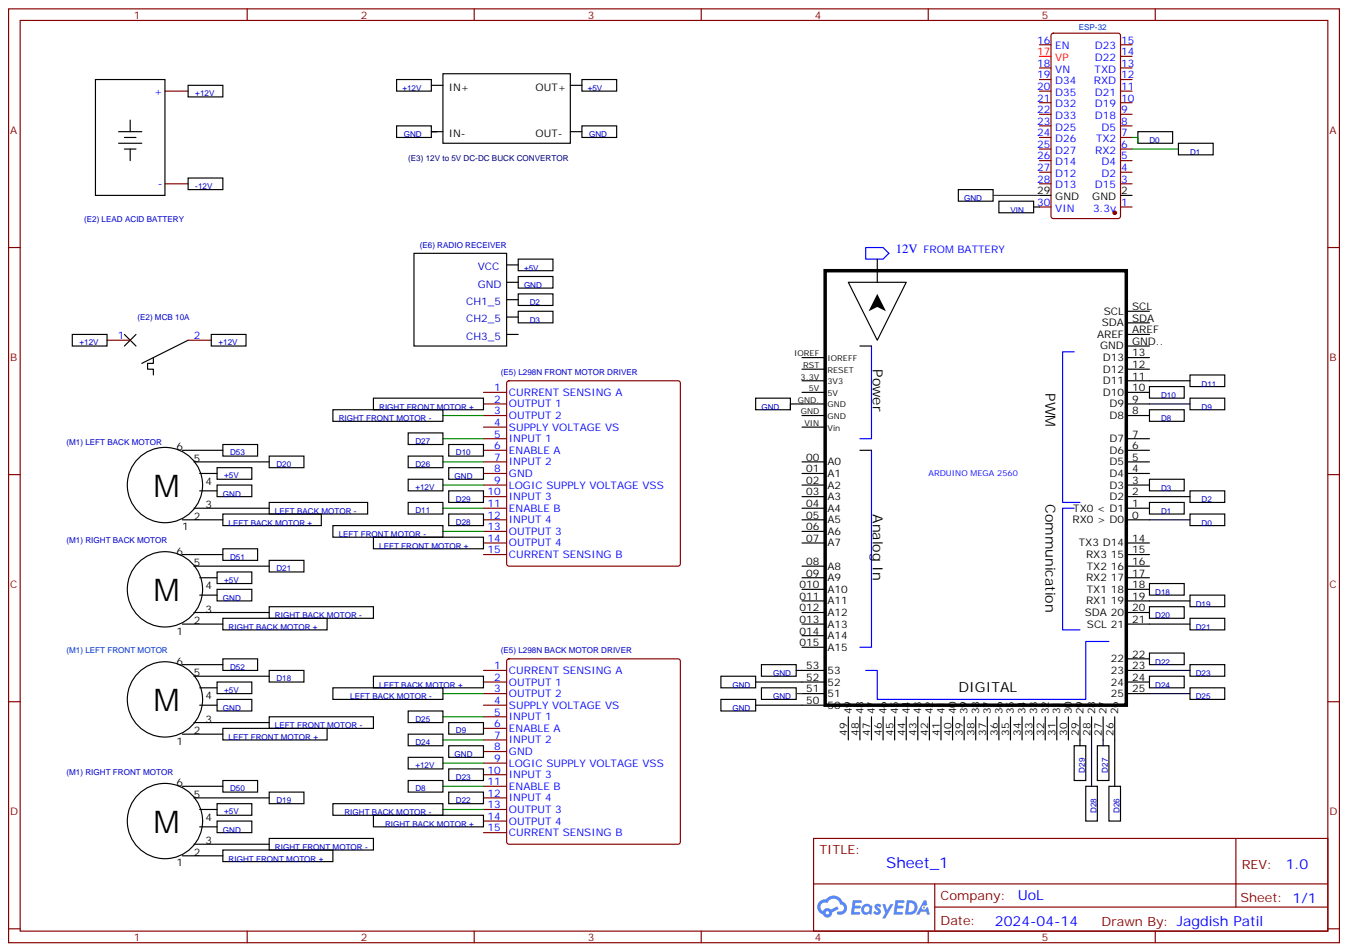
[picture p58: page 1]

(E3) 12V to 5V DC-DC BUCK CONVERTOR

Drawn By: Jagdish Patil

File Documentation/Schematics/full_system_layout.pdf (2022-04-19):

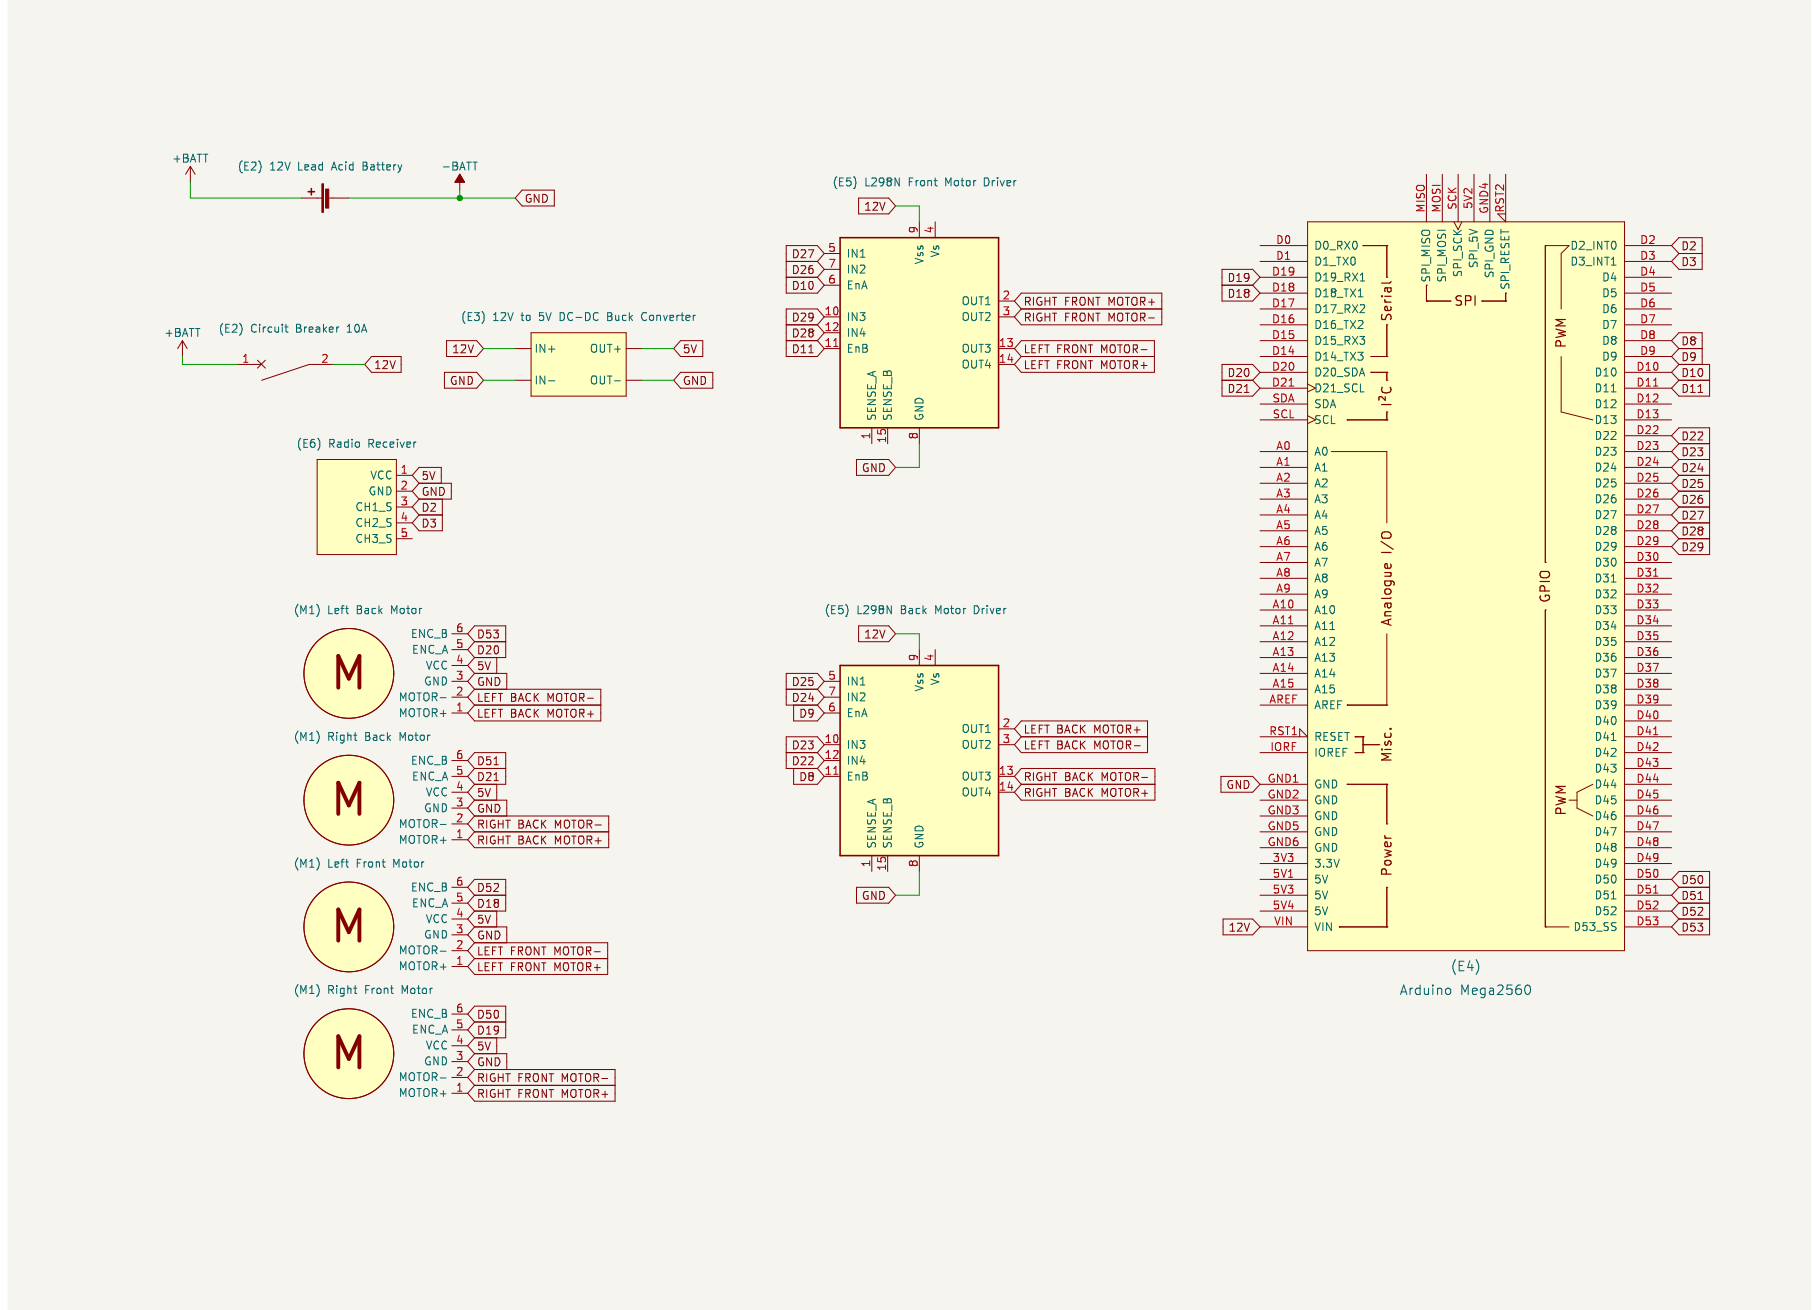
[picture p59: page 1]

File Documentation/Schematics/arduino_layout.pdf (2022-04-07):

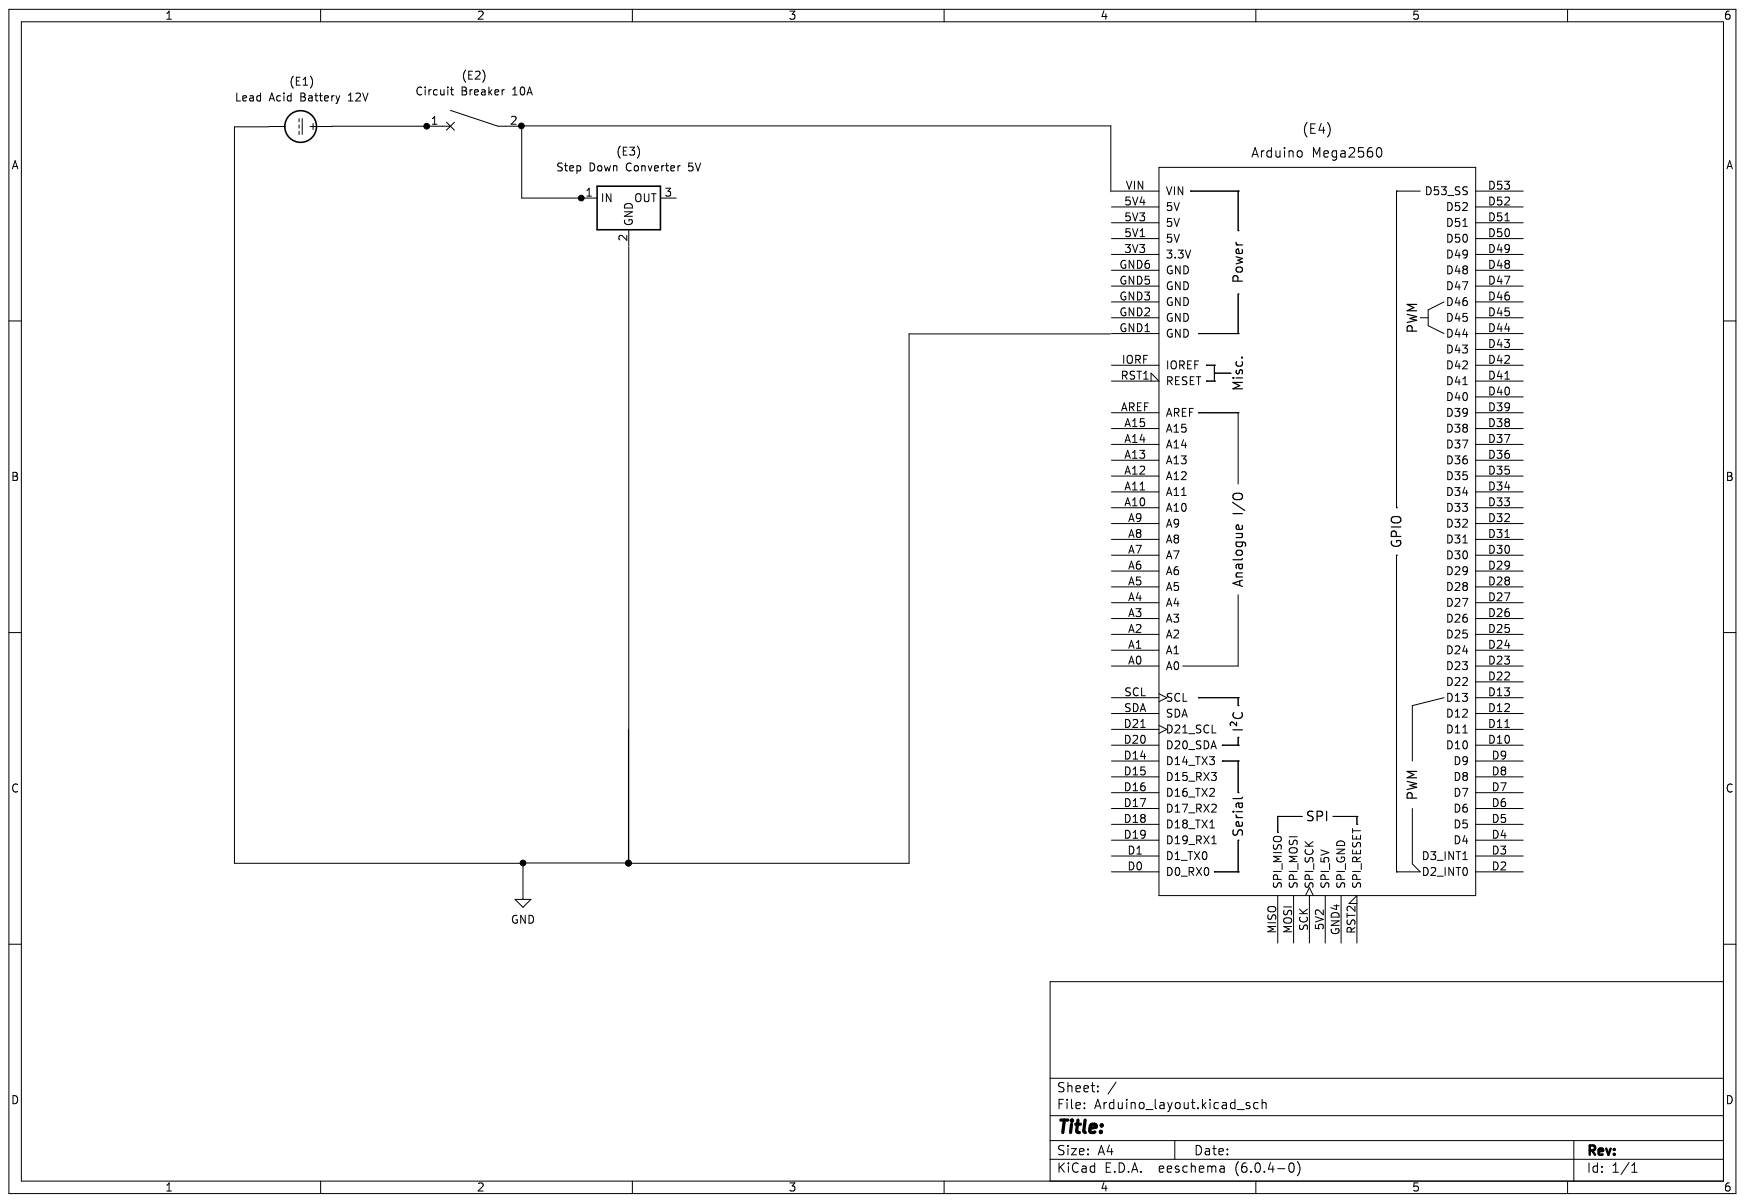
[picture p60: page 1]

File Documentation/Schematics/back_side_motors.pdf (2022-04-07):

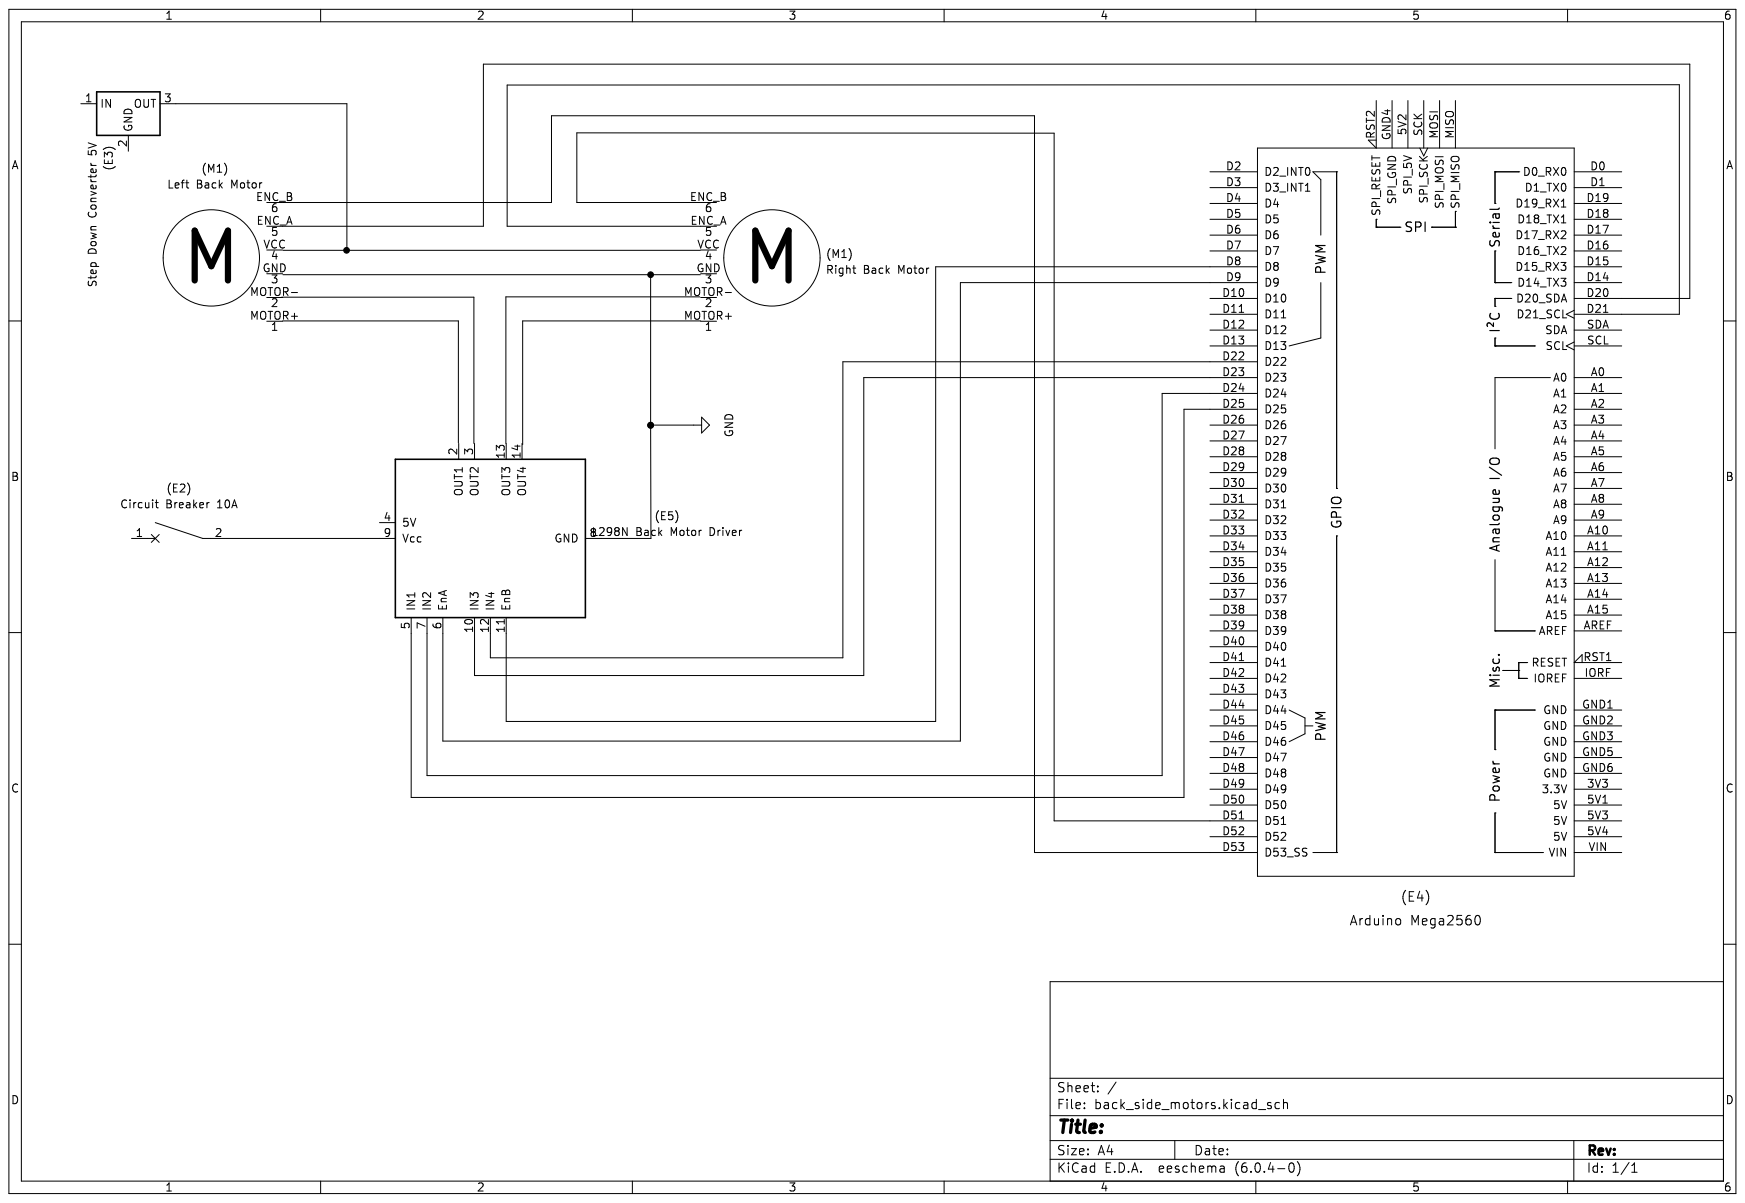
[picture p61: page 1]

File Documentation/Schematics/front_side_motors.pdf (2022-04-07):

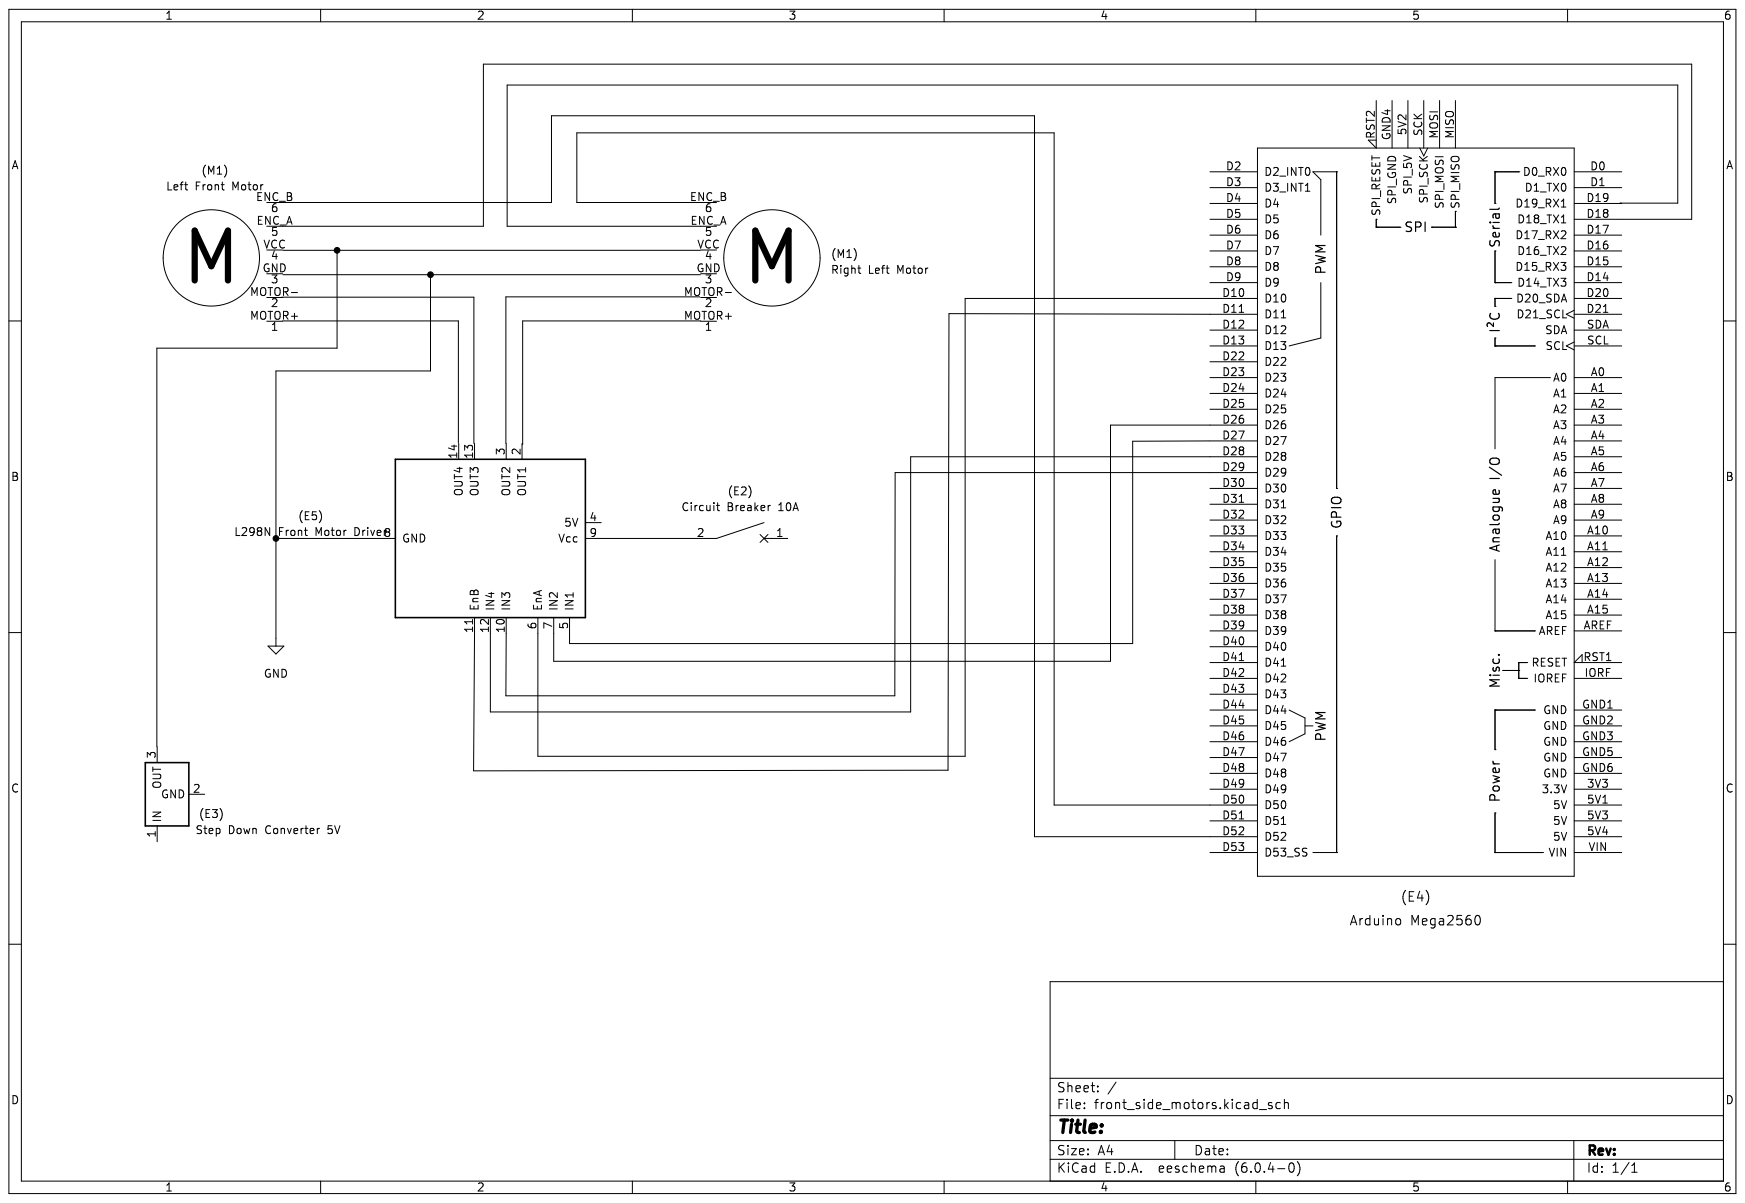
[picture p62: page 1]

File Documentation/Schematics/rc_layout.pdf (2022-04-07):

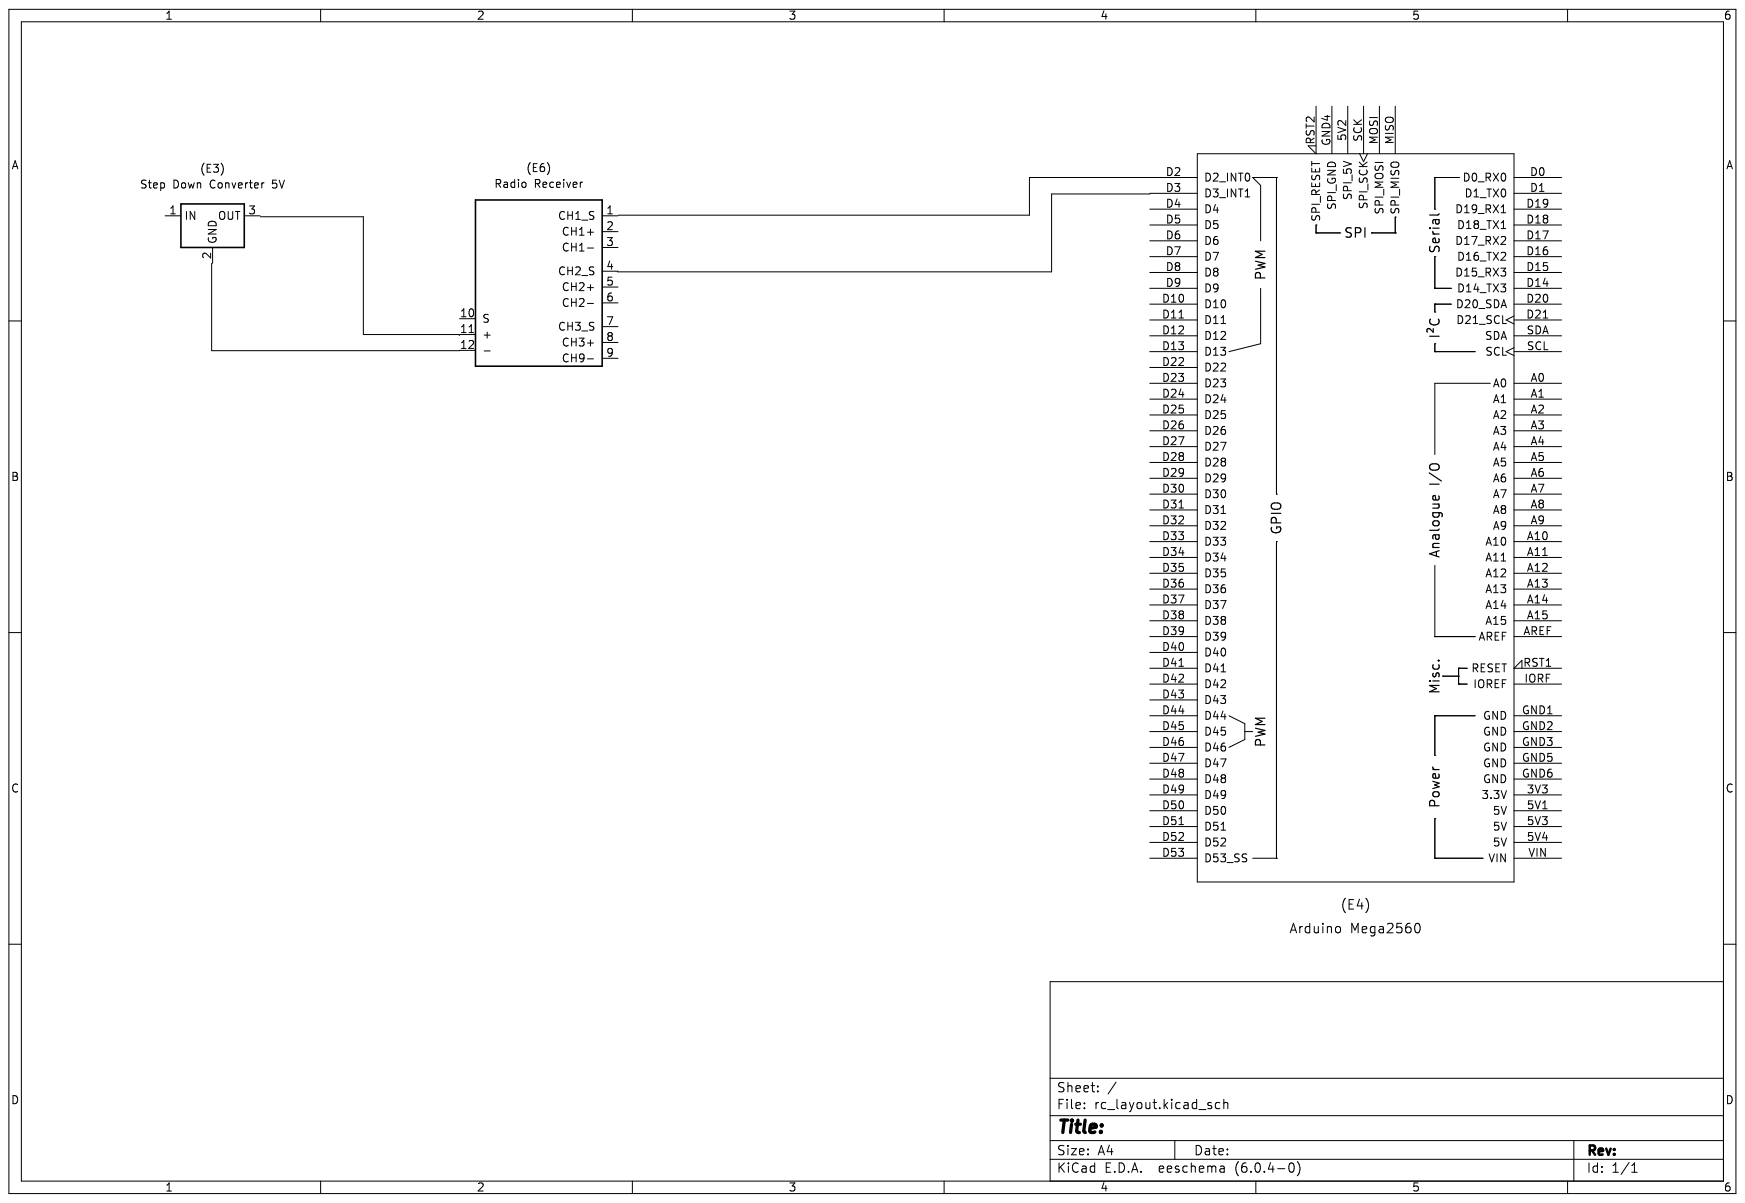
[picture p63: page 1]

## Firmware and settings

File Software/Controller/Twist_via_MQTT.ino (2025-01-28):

#include <util/atomic.h>
#include <WiFi.h>
#include <PubSubClient.h>
#include <ArduinoJson.h>        // For parsing JSON input


#define NMOTORS 4

#define UMAX 255
#define PGAIN 2
#define DGAIN 0.015
#define IGAIN 5
#define VMAX 12

// WiFi settings
char ssid[] = "";  // Network SSID
char pass[] = "";  // WPA key

// MQTT Broker settings
const char *mqtt_broker = "broker.emqx.io"; // EMQX broker endpoint
const char *mqtt_topic = "Robot/velocity"; // MQTT topic
const char *mqtt_username = "emqx"; // MQTT username for authentication
const char *mqtt_password = "public"; // MQTT password for authentication
const int mqtt_port = 1883; // MQTT port (TCP)

WiFiClient wifiClient;
PubSubClient mqtt_client(wifiClient);

void connectToWiFi();
void connectToMQTTBroker();
void mqttCallback(char *topic, byte *payload, unsigned int length);
void processTwistMessage(const char *payload);




// Declare Pins
// RB, LB, RF, LF
const int ENC_A[] = {21,20,19,18};
const int ENC_B[] = {51,53,50,52};
const int PWM[] = {8,9,10,11};
const int INP_1[] = {22,24,27,29};
const int INP_2[] = {23,25,26,28};

//const double maxRPS = 9.0; // maximum rads per second
const float linearMax = 1.0;
const float angularMax = 1.5;



// volatile variables (in encoder callback)
volatile long pos_i[] = {0,0,0,0};


long previous_pos[] = {0,0,0,0};
float velocity[] = {0,0,0,0};
long prevT = 0;
float deltaT = 0;

// Robot variables
int N = 1440;
double wheelRadius = 0.056; // m
double wheelDistance = 0.395; // m

int joyValue = 0;
float steeringValue;
float throttleValue;
float targetSpeed[] = {0,0,0,0};
float currentSpeed[] = {0,0,0,0};
float previousSpeed[] = {0,0,0,0};

// A class to compute the control signal
class SimplePID{
  private:
    float kp, kd, ki, umax; // Parameters
    float eprev, eintegral; // Storage

  public:
  // Constructor
  SimplePID() : kp(2), kd(1), ki(5), umax(15), eprev(0.0), eintegral(0.0){}

  // A function to set the parameters
  void setParams(float kpIn, float kdIn, float kiIn, float umaxIn){
    kp = kpIn; kd = kdIn; ki = kiIn; umax = umaxIn;
  }

  // A function to compute the control signal
  void evalu(float value, float target, float deltaT, int &pwr, int &dir){
    // error
    float e = target - value;
  
    // derivative
    float dedt = (e-eprev)/(deltaT);
  
    // integral
    eintegral = eintegral + (0.5*(eprev+e)*deltaT); // 1/2 * (a + b) * h
  
    // control signal
    float u = kp*e + kd*dedt + ki*eintegral;

    // motor direction
    dir = 1;
    if(u<0){
      dir = -1;
    }

    // motor power
    pwr = int(255 * (abs(u)/VMAX));
    if( pwr > umax ){
      pwr = umax;
    } else if ( pwr < 20) {
      pwr = 0;
    }

    if (eintegral > 10) {
      eintegral = 10;
    } else if (eintegral < -10) {
      eintegral = -10;
    }
    
    // store previous error
    eprev = e;

    //Serial.print(e);
    //Serial.print('\t');
    //Serial.print(eintegral);
    //Serial.println();
  }
  
};

// PID class instances
SimplePID motor[NMOTORS];

void setMotor(int dir, int PWMVal, int PWM, int INP_1, int INP_2){
  analogWrite(PWM,PWMVal);
  if(dir == 1){
    digitalWrite(INP_1,LOW);
    digitalWrite(INP_2,HIGH);
  }
  else if(dir == -1){
    digitalWrite(INP_1,HIGH);
    digitalWrite(INP_2,LOW);
  }
  else{
    digitalWrite(INP_1,LOW);
    digitalWrite(INP_2,LOW);
  }


}

template <int j>
void readEncoder(){
  int b = digitalRead(ENC_B[j]);
  int i = 0;
  if ((j == 0) || (j == 2)) { 
    if(b > 0){
      pos_i[j]++;
    }
    else{
      pos_i[j]--;
    }
  } else if ((j == 1) || (j == 3)) {
    if(b > 0){
      pos_i[j]--;
    }
    else{
      pos_i[j]++;
    }
  }
}

volatile int count = 0;
int count_prev = 0;

ISR(TIMER5_COMPA_vect) {
  count++;
}

void setup() {
  
  Serial.begin(115200);
  connectToWiFi();
  mqtt_client.setServer(mqtt_broker, mqtt_port);
  mqtt_client.setCallback(mqttCallback);
  connectToMQTTBroker();

  //Setup timer interrupt using timer 5
  cli();
  TCCR5A = 0;
  TCCR5B = 0;
  TCNT5 = 0;
  OCR5A = 12499; //Prescaler = 64
  TCCR5B |= (1 << WGM12);
  TCCR5B |= (1 << CS11 | 1 << CS10);
  TIMSK5 |= (1 << OCIE5A);
  sei(); // re-enables interrupts

  for(int k = 0; k < NMOTORS; k++){
    pinMode(ENC_A[k],INPUT);
    pinMode(ENC_B[k],INPUT);
    pinMode(PWM[k],OUTPUT);
    pinMode(INP_1[k],OUTPUT);
    pinMode(INP_2[k],OUTPUT);
    
 //   motor[k].setParams(500, 70, 20, 255);
    //motor[k].setParams(70,0.1,5,255);
    motor[k].setParams(PGAIN,DGAIN,IGAIN,UMAX);
  }

  attachInterrupt(digitalPinToInterrupt(ENC_A[0]),readEncoder<0>,RISING);
  attachInterrupt(digitalPinToInterrupt(ENC_A[1]),readEncoder<1>,RISING);
  attachInterrupt(digitalPinToInterrupt(ENC_A[2]),readEncoder<2>,RISING);
  attachInterrupt(digitalPinToInterrupt(ENC_A[3]),readEncoder<3>,RISING);

}

void connectToWiFi() {
    Serial.println("Connecting to WiFi");
    WiFi.begin(ssid, pass);
    while (WiFi.status() != WL_CONNECTED) {
        delay(500);
        Serial.print(".");
    }
    Serial.println("\nConnected to the WiFi network");
}

void connectToMQTTBroker() {
    while (!mqtt_client.connected()) {
        String client_id = "arduino-mega-client"; // Change to esp32-client for clarity
        Serial.print("Connecting to MQTT Broker as ");
        Serial.println(client_id); // Correct usage of Serial.println
        if (mqtt_client.connect(client_id.c_str(), mqtt_username, mqtt_password)) {
            Serial.println("Connected to MQTT broker");
            mqtt_client.subscribe(mqtt_topic);
            // Publish message upon successful connection
           // mqtt_client.publish(mqtt_topic, "publish any message here");
        } else {
            Serial.print("Failed to connect to MQTT broker, rc=");
            Serial.print(mqtt_client.state());
            Serial.println(" try again in 5 seconds");
            delay(5000);
        }
    }
}

void mqttCallback(char *topic, byte *payload, unsigned int length) {
    Serial.print("Message received on topic: ");
    Serial.println(topic);

    // Convert payload (byte array) to a String
    String msg;
    for (unsigned int i = 0; i < length; i++) {
        msg += (char)payload[i];
    }

    Serial.print("Message: ");
    Serial.println(msg);
    Serial.println("-----------------------");

    // Pass the message as a C-string
    processTwistMessage(msg.c_str());
}



float mapf(float x, float in_min, float in_max, float out_min, float out_max) {
     float result;
     result = (x - in_min) * (out_max - out_min) / (in_max - in_min) + out_min;
     return result;
}



void loop() {
    if (!mqtt_client.connected()) {
        connectToMQTTBroker();
    }
    mqtt_client.loop();

  // T = 0.05s
  if (count > count_prev) {
    // Compute time
    long currT = micros();
    float deltaT = ((float) (currT-prevT))/1.0e6;


      
    float delta_pos[] = {0.0, 0.0, 0.0, 0.0};
  
    // Read the velocity in an atomic block to avoid a potential misread
    // and convert from counts/s to rad/s
    ATOMIC_BLOCK(ATOMIC_RESTORESTATE){
      for (int k=0; k<NMOTORS; k++){
        delta_pos[k] = pos_i[k] - previous_pos[k];
        velocity[k] = delta_pos[k] / N / deltaT * 2 * PI;
        previous_pos[k] = pos_i[k];
      }
    }
    
    // Read transmitter
    ATOMIC_BLOCK(ATOMIC_RESTORESTATE){


      throttleValue = 0.5;
      steeringValue = 0;


      // Make a dead-zone for throttling
      if ((throttleValue >= -0.10) && (throttleValue <= 0.10)) {
        throttleValue = 0.0;
      }
      // Make a dead-zone for steering
      if ((steeringValue >= -0.25) && (steeringValue <= 0.25)) {
        steeringValue = 0.0;
      }
    }


    // Reset Speeds
    targetSpeed[0] = 0.0;
    targetSpeed[2] = 0.0;
    targetSpeed[1] = 0.0;
    targetSpeed[3] = 0.0;

    Serial.print(throttleValue);
    Serial.print('\t');
    Serial.println(steeringValue);

    // if controller is off when robot is turned on. throttleValue received is ~ -3. Going to reset this to zero
    if (throttleValue < -1.5) {
      throttleValue = 0.0;
    }

    // if controller is off when robot is turned on. steeringValue received is ~ 3. Going to reset this to zero
    if (steeringValue > 1.5) {
      steeringValue = 0.0;
    }

    // Map desired speed to motor speeds
    float linearSpeed = linearMax * throttleValue;
    //linearSpeed = 0.0;
    float angularSpeed = angularMax * steeringValue;
    //float angularSpeed = 0.0;
    //float rightSpeed = (1/wheelRadius) * linearSpeed - (wheelDistance/wheelRadius) * angularSpeed;
    //float leftSpeed = (1/wheelRadius) * linearSpeed + (wheelDistance/wheelRadius) * angularSpeed;

    float rightSpeed = ((linearSpeed + (wheelDistance * angularSpeed)) / wheelRadius);
    float leftSpeed = ((linearSpeed - (wheelDistance * angularSpeed)) / wheelRadius);

    
    targetSpeed[0] = rightSpeed;
    targetSpeed[2] = rightSpeed;
    targetSpeed[1] = leftSpeed;
    targetSpeed[3] = leftSpeed;
    

    
    
    // Low-pass filter (25 Hz cutoff)
    for (int k=0; k<NMOTORS; k++) {
      currentSpeed[k] = 0.854*currentSpeed[k] + 0.0728*velocity[k] + 0.0728*previousSpeed[k];
      previousSpeed[k] = velocity[k];
    }

    
    // Set speeds
    for (int k=0; k<NMOTORS; k++) {
      int pwr, dir;
      motor[k].evalu(velocity[k], targetSpeed[k], deltaT, pwr, dir);

      if ((targetSpeed[k] < 0.1) && (targetSpeed[k] > -0.1) ) {
        pwr = 0;
        dir = 0;
      }
      setMotor(dir, pwr, PWM[k], INP_1[k], INP_2[k]);
    }

    // RB, LB, RF, LF

    // calculate forward kinematics from read wheel velocities
    float rightVirtualWheelSpeed = (velocity[0] + velocity[2]) * 0.5;
    float leftVirtualWheelSpeed = (velocity[1] + velocity[3]) * 0.5;

    float feedbackAngularVelocity = (((rightVirtualWheelSpeed * wheelRadius) + ( -1* leftVirtualWheelSpeed * wheelRadius)) / ( 2 * wheelDistance));
    



    prevT = currT;
    count_prev = count;
  }

}


// Process the incoming twist message and parse the linear and angular velocities
void processTwistMessage(const char *payload) {
  StaticJsonDocument<200> doc;
  DeserializationError error = deserializeJson(doc, payload);

  if (!error) {
    float linear_x = doc["linear"]["x"];
    float linear_y = doc["linear"]["y"];
    float linear_z = doc["linear"]["z"];
    float angular_x = doc["angular"]["x"];
    float angular_y = doc["angular"]["y"];
    float angular_z = doc["angular"]["z"];

    // For this robot, we care only about the x component of linear and z component of angular velocity
    throttleValue = linear_x;  // Linear velocity (x-axis)
    steeringValue = angular_z; // Angular velocity (z-axis)

    // Print out the velocities to the Serial Monitor
    Serial.print("Throttle (linear x): ");
    Serial.println(throttleValue);
    Serial.print("Steering (angular z): ");
    Serial.println(steeringValue);
  } else {
    Serial.println("Error parsing JSON");
  }
}

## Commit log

2022-04-05 Add documentation for robot with hinge
2022-04-05 Fix typo in motor_and_wheels.md
2022-04-06 Add wiring documentation
2022-04-06 update bracket image
2022-04-07 update motor bracket instruction
2022-04-07 update motor image
2022-04-07 update corner bracket image
2022-04-07 add build time to each assembly
2022-04-19 update images location and cad file
2022-04-19 update assembly instructions
2022-04-19 update assembly times
2022-04-21 added arduino firmware
2022-04-21 Add pid docs
2022-05-01 add main cad files and instructions
    [Acrylic Spacer.dxf, Back_back_340_200.dxf, Back_middle_340_200_DXF.dxf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]
2024-11-25 Update and rename hi.txt to Simple Robot in World.sdf
    [Simple Robot in World.sdf]
2024-11-25 Update Simple Robot in World.sdf
    Building simple robot by following this tutorial:
    https://gazebosim.org/docs/latest/building_robot/
    #This Update is exactly the same tutorial provided.
    [Simple Robot in World.sdf]
2024-11-25 Update Simple Robot in World.sdf
    Creating simple robot by following this tutorial:
    #This update is exactly the same tutorial provided.
    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
    [Simple Robot in World.sdf]
2024-12-04 Create MovingOpenScout
    1) On the way to have Open Scout visualization "4 wheels"
    2) Move the Robot using plugin with the command below:
    gz topic -t "/cmd_vel" -m gz.msgs.Twist -p "linear: {x: 0.0}, angular: {z: 0.0}"
    Next step:
    1) Improve the visualization "2 Boxes"
    2) Adjust the physical parameters such as mass, inertia for the wheels and the chassis itself.
2024-12-12 moving OpenScout
    Uodates on MovingOpenScout
    3) Move the Robot using plugin with arrrows
    4) Adjust the physical parameters such as size of box and wheels.
    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
2024-12-13 Create Twist_via_MQTT.ino
    this is an untested code to recive twisr messages via a public MQTT broker and parse the variables into a format usable by a PID controller for Open scout
    [Twist_via_MQTT.ino]
2024-12-14 Add files via upload
    Open Scout CAD in stl format
    [OpenScoutCAD.stl]
2025-01-11 OpenScout SDF
    use mesh files (stl format)
    front chassis
    back chassis
    front left wheel
    front right wheel
    back left wheel
    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
    [OpenScout.sdf, OpenScout_FE.sdf, OpenScout_FE_one_chassis.sdf]
2025-01-22 Added the openscout ros2 package
    a package containing a virtual model of the openscout, running in gazebo harmonic, within a ros2 package.
    [BackLeftWheel.stl, BackRightWheel.stl, FrontLeftWheel.stl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]

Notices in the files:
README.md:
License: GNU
